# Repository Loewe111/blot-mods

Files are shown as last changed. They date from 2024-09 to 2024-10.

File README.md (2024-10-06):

# My Blot Mods

This is a collection of modifications I've made to my [Blot](https://github.com/hackclub/blot/), a Plotter by Hackclub.

- [Tidy Cable Management](#tidy-cable-management)
- [Limit Switches](#limit-switches)
- [Laser Blot](#laser-blot)

## Tidy Cable Management

I just printed these [Cable Clips](https://www.thingiverse.com/thing:6466108) and secured the cables to it with zip ties.

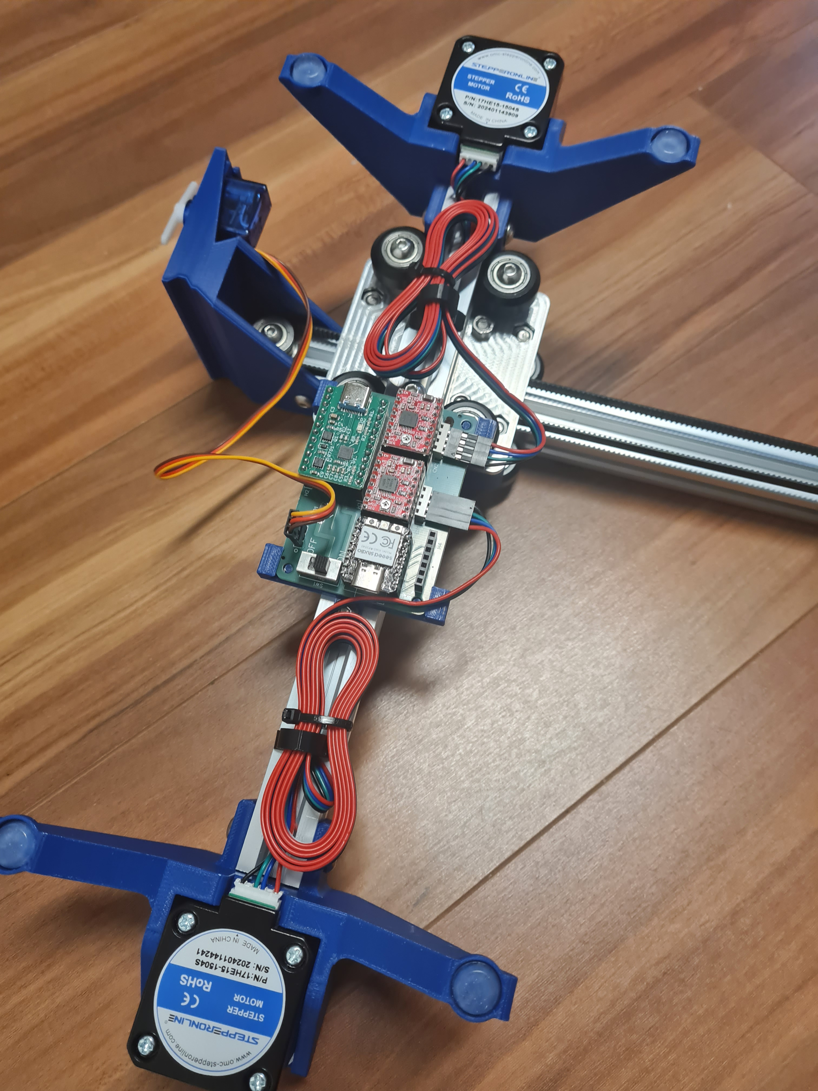
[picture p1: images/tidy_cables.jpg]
Cable Clips


## Limit Switches

This adds a pair of limit switches to the blot, utilizing the header of pins on the PCB.

### Parts

| Quantity | Name | Image |
| --- | --- | --- |
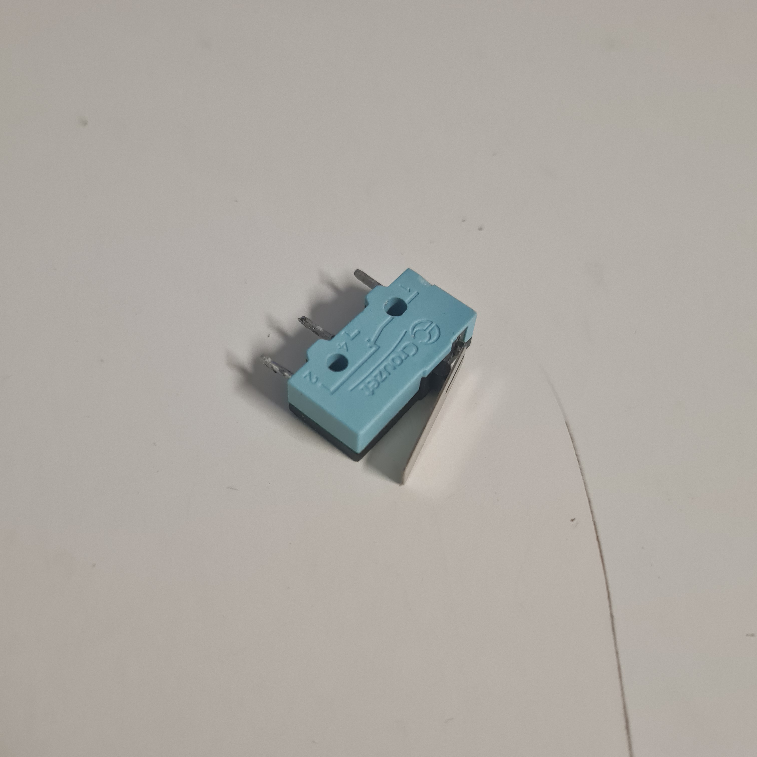
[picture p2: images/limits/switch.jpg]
Limit Switch
| 2 | Limit Switch / Microswitch |  |
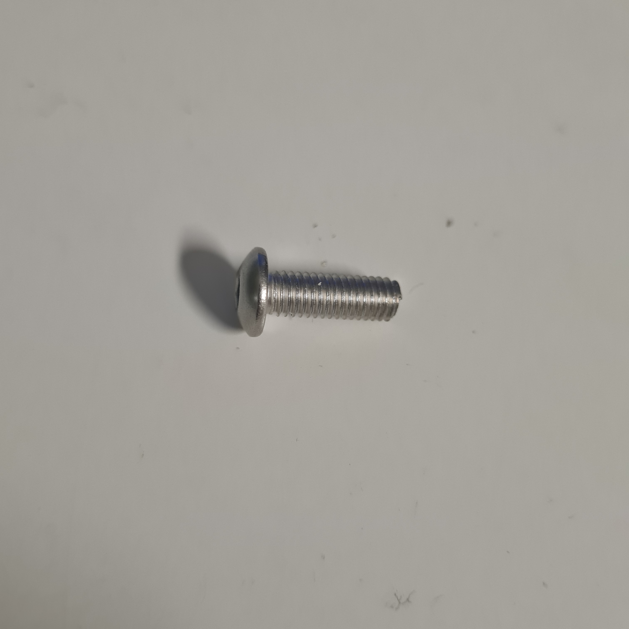
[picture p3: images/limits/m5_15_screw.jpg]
M5x15 Screw
| 1 | M5x15 Screw |  |
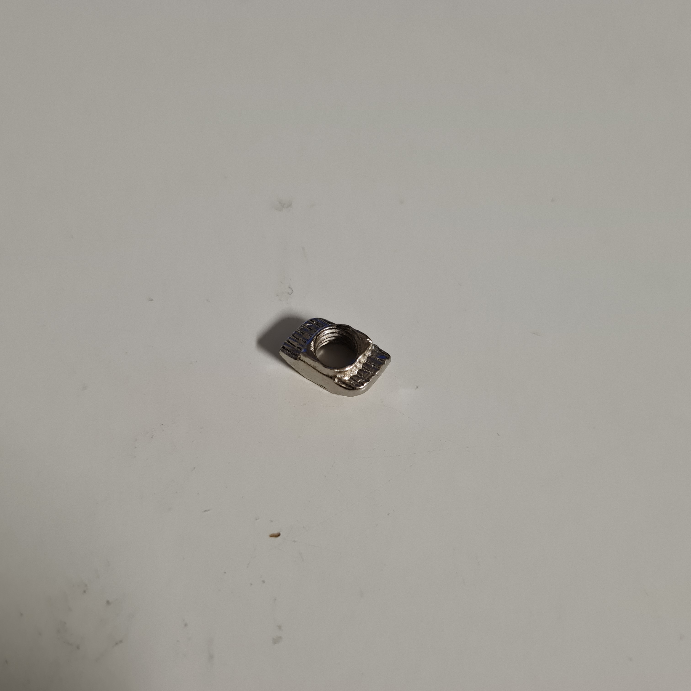
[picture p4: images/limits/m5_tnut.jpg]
M5 T-Nut
| 1 | M5 T-Nut |  |
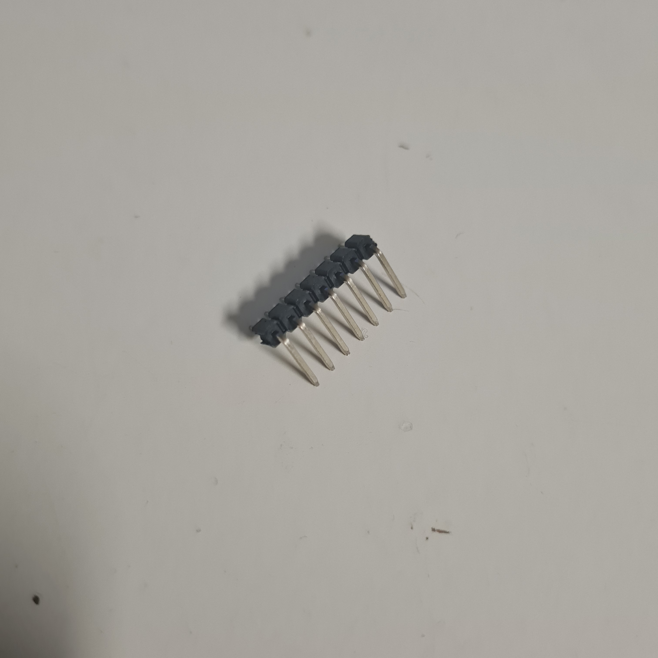
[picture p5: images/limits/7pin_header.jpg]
1x7 Angled Header
| 1 | 1x7 Angled Header |  |
| 4 | ca. 20cm Wire | |
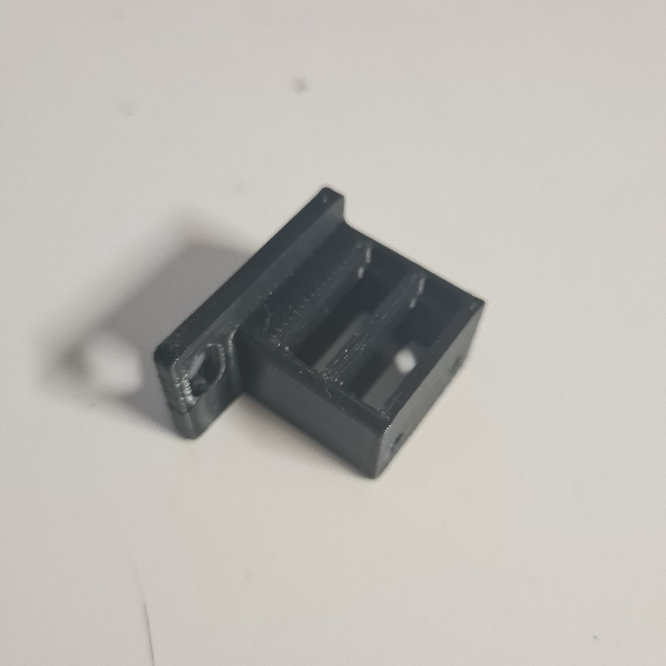
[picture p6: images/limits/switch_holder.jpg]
3D Printed Mount
| 1 | 3D Printed Mount [(here)](models/endstop_mount.stl) |  |
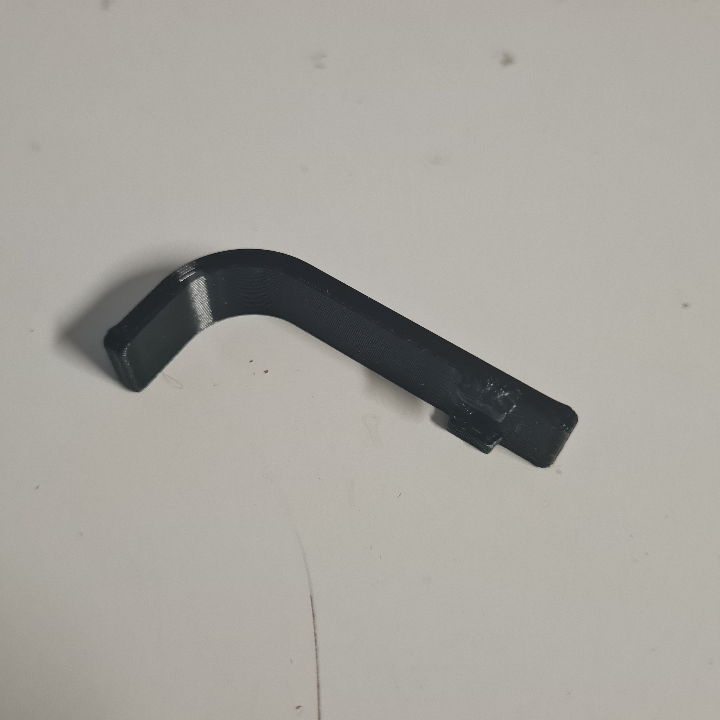
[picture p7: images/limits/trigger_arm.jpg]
3D Printed Arm
| 1 | 3D Printed Arm [(here)](models/endstop_arm.stl) |  |

### Assembly

1. Insert the Limit Switches into the 3D Printed Mount. Make sure the springs face the right direction. Like this:

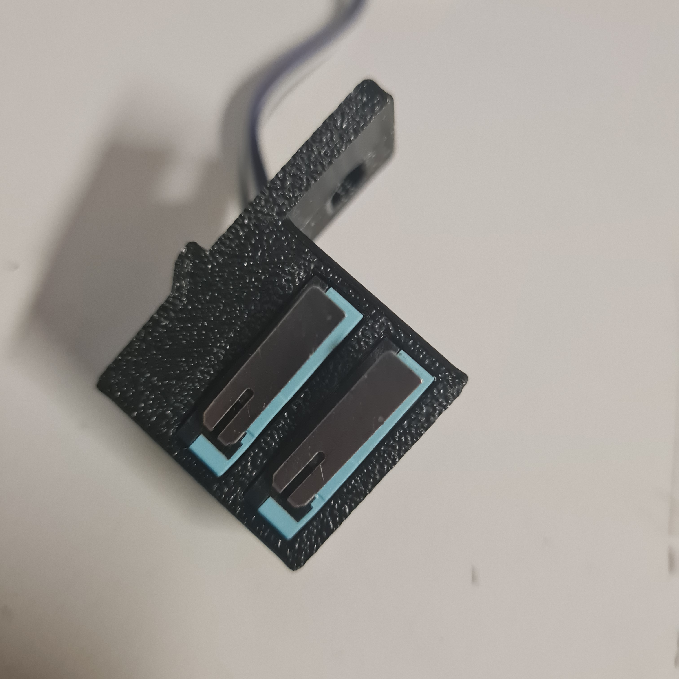
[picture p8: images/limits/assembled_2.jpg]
Assembled
    
2. Solder the Wires to the COM and NC pins of the Limit Switches.
    It should look like this:

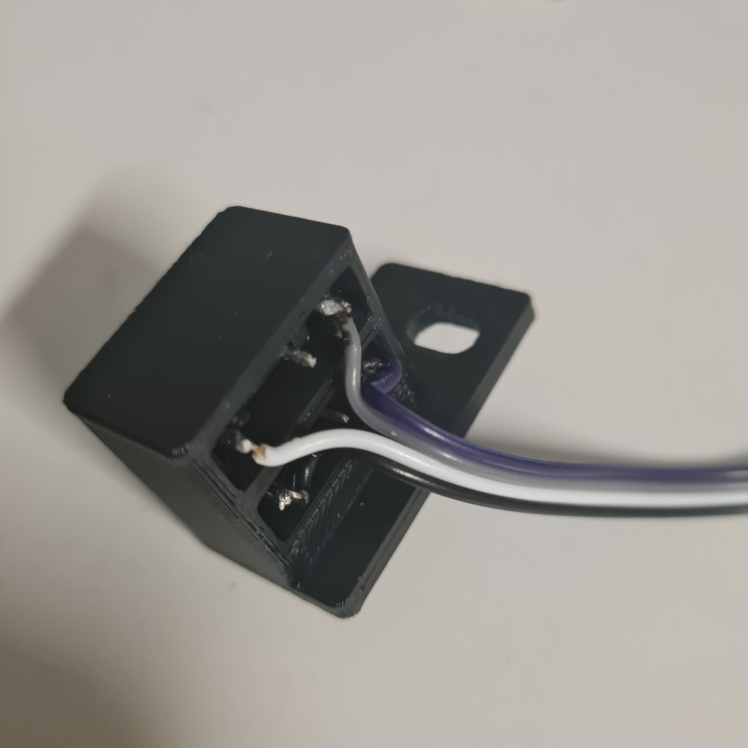
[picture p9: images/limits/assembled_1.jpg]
Wiring
    
3.  Solder the other ends of the wires to the 1x7 Angled Header. The COM pins both connect to 7th pin, the NC pin of the Lower (X) Limit Switch connects to the 3rd pin, and the NC pin of the Upper (Y) Limit Switch connects to the 4th pin.

    Motor Mount
4. Remove the top screw of the left motor mount.

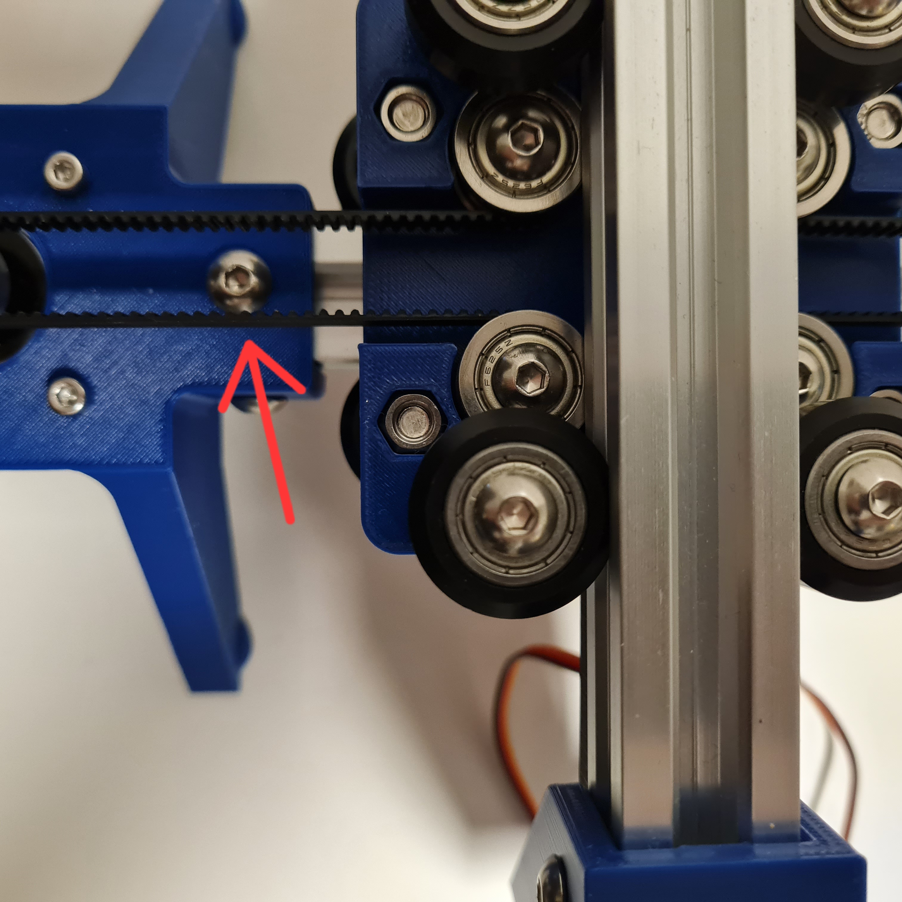
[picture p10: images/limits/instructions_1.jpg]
    

    Then, put the 3D Printed Mount on top of the motor mount and screw it in place with the M5x15 (Keep the old screw for the next step). Adjust the position of the Limit Switches so it gets triggered before the gantry hits the end of the plotter.

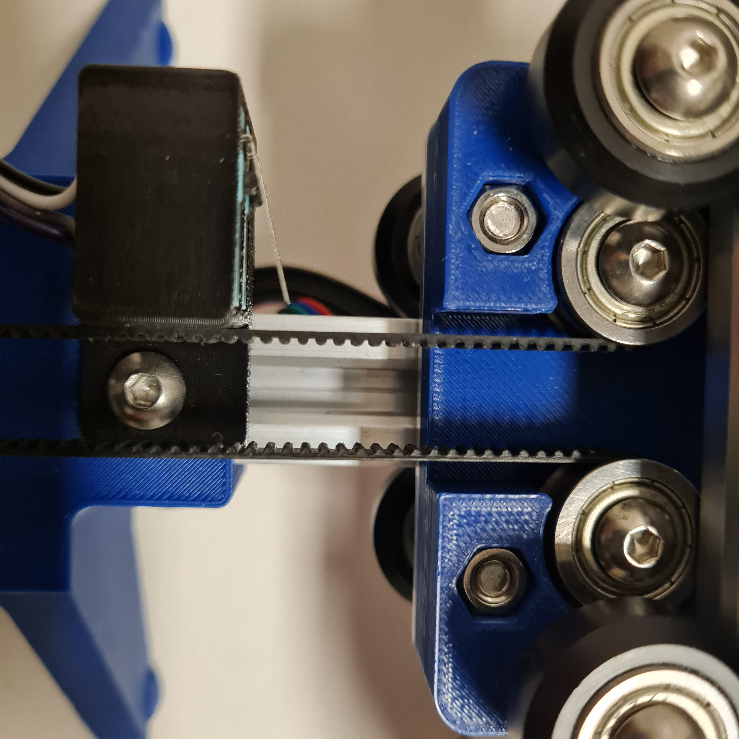
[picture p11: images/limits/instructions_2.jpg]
    
5. Attach the 3D Printed Arm to top extrusion with the M5 T-Nut and the M5x10 screw that you removed in the last step.

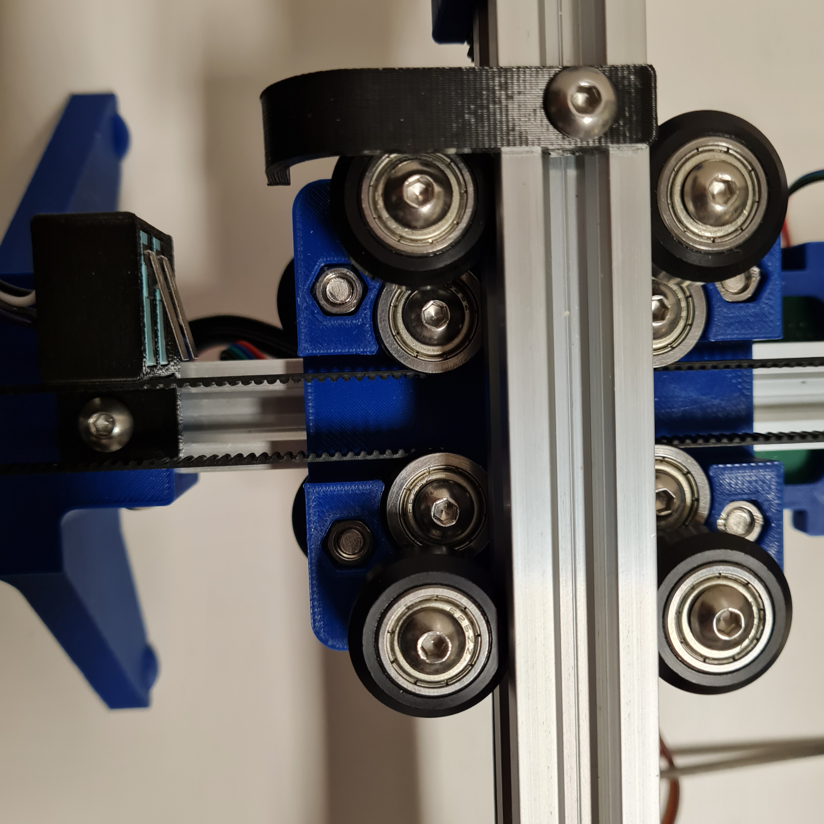
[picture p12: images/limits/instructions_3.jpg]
    

    Make sure that when the gantry is at the limit switch, that the arm also triggers the switch before it hits the end of the plotter.
6. Plug the connector into the header on the PCB.

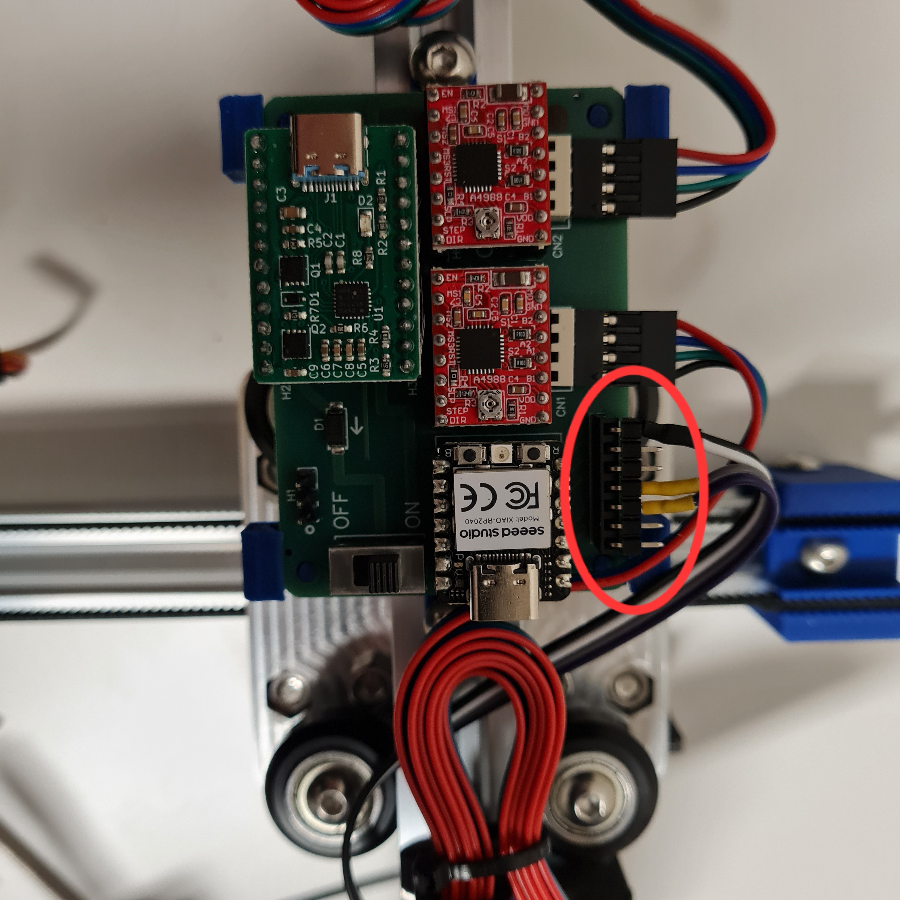
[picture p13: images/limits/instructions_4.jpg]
    

    Make sure the wires are not in the way of the gantry.

That's it!

### Firmware

I have created a grblHAL driver for the Blot. You can find it [here](https://github.com/Loewe111/grblHAL-blot). The only limitation is that it cant use the Servo for the pen lift.

I plan to modify the original firmware to support the limit switches as well.

## Laser Blot

I also added a 5.5W Diode Laser to my Blot. With this I am able to engrave wood, plastics and even acrylics, aswell as cutting paper and some thin wood.

> [!CAUTION]
> Lasers are dangerous! Always wear appropriate eye protection!

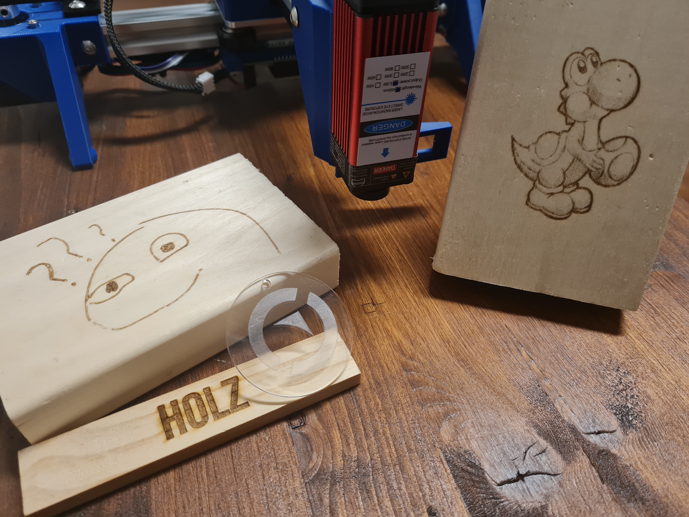
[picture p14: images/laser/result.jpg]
Result


### Parts

| Quantity | Name | Image |
| --- | --- | --- |
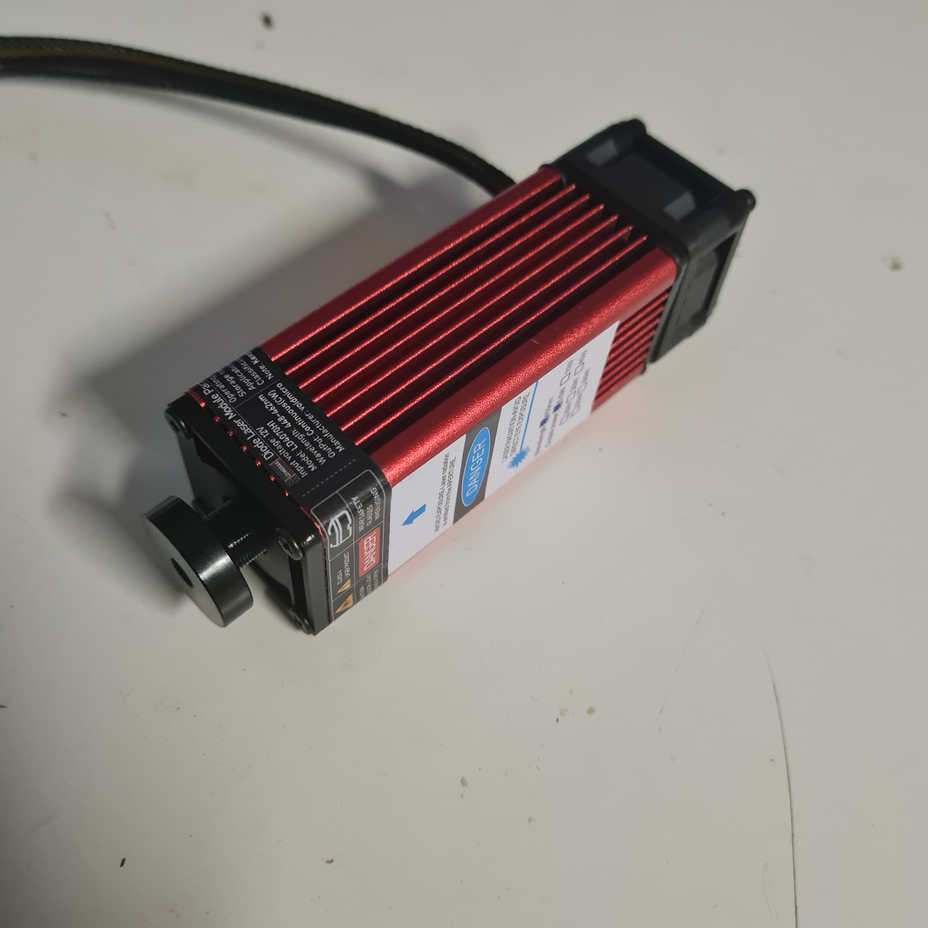
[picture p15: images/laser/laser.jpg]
Laser Module
| 1 | Laser Module (I got [this 5.5W one](https://de.aliexpress.com/item/1005003710714783.html)) |  |
| 1 | Laser Safety Glasses (I got [these](https://www.amazon.de/dp/B0CS6DHZRP)) | |
| 1 | A 12V Power Supply | |
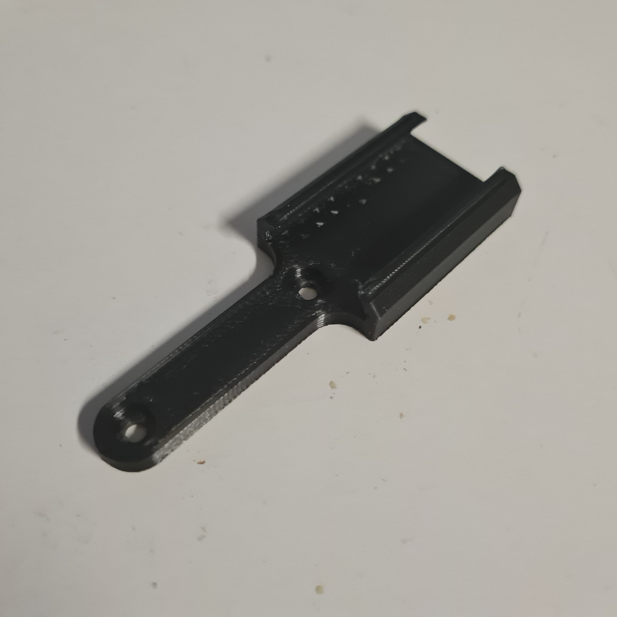
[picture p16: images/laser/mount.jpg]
3D Printed Laser Mount
| 1 | 3D Printed Laser Mount [(here)](models/laser_mount.stl) |   |
| 1 | 12V Barrel Plug (Or other connector for the power supply) | |
| 1 | JST-XH 3 Pin Connector | |
| 1 | 3 Pin Female Header or Crimp Connector | |
| | Some Wires | |

### Assembly

1. Attach the Laser Module to the 3D Printed Mount with the screws that came with the laser.

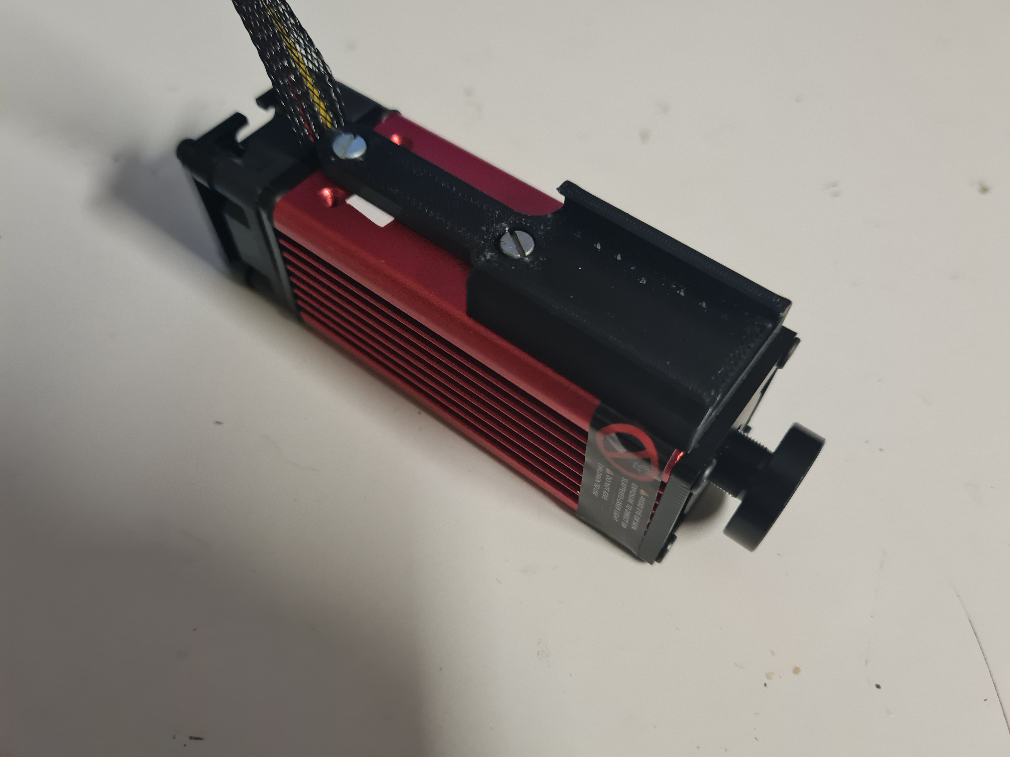
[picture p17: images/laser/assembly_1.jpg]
Laser Assembly
    

2. Create the wiring harness for the laser, by connecting the JST Connector to the Barrel Plug and the 3 Pin Connector as shown in the diagram below.

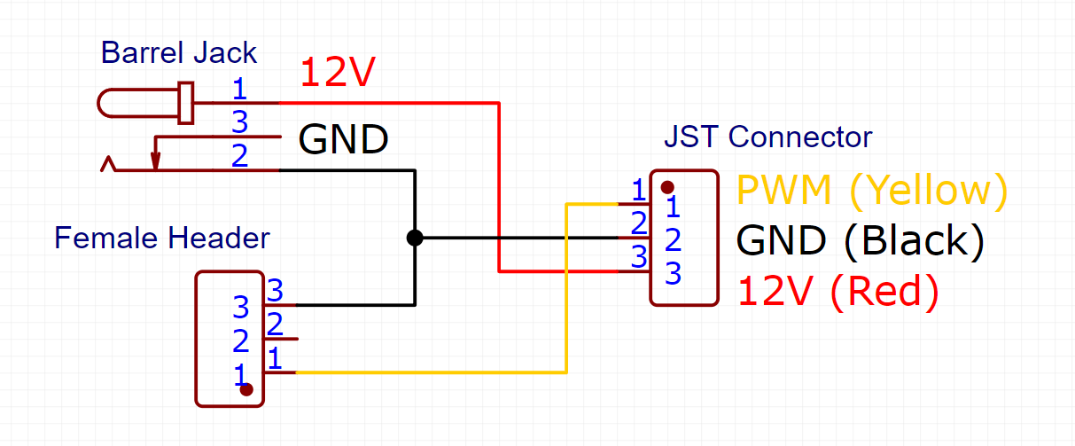
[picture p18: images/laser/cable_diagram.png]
Laser Wiring
    

    My harness looks like this:

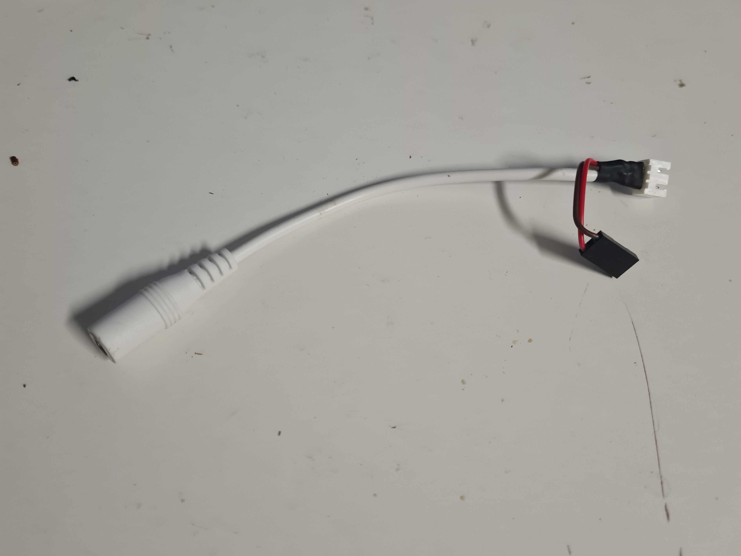
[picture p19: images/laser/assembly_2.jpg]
Laser Wiring
    

3. Connect the 3 Pin Female Header to the Pin Header on the PCB, where the Servo was connected. Make sure that the GND pin is on the side with the white dot.

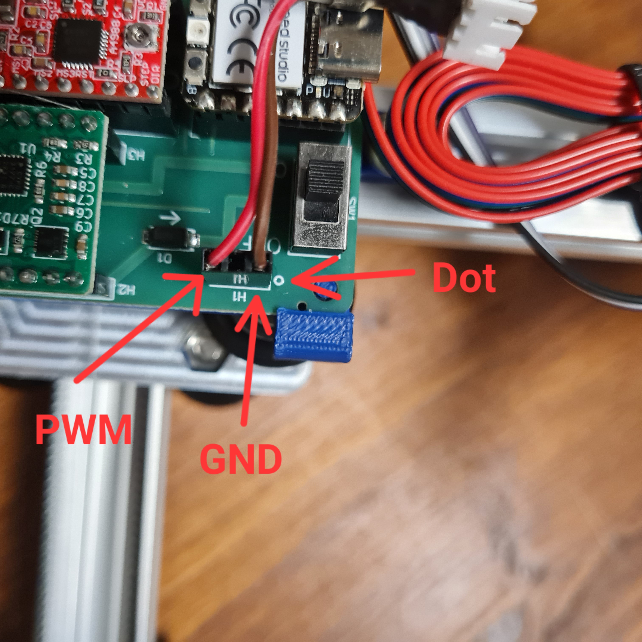
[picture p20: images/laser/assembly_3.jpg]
Laser Wiring
    

4. Attach the Laser to the Arm, where the Pen Holder was attached.

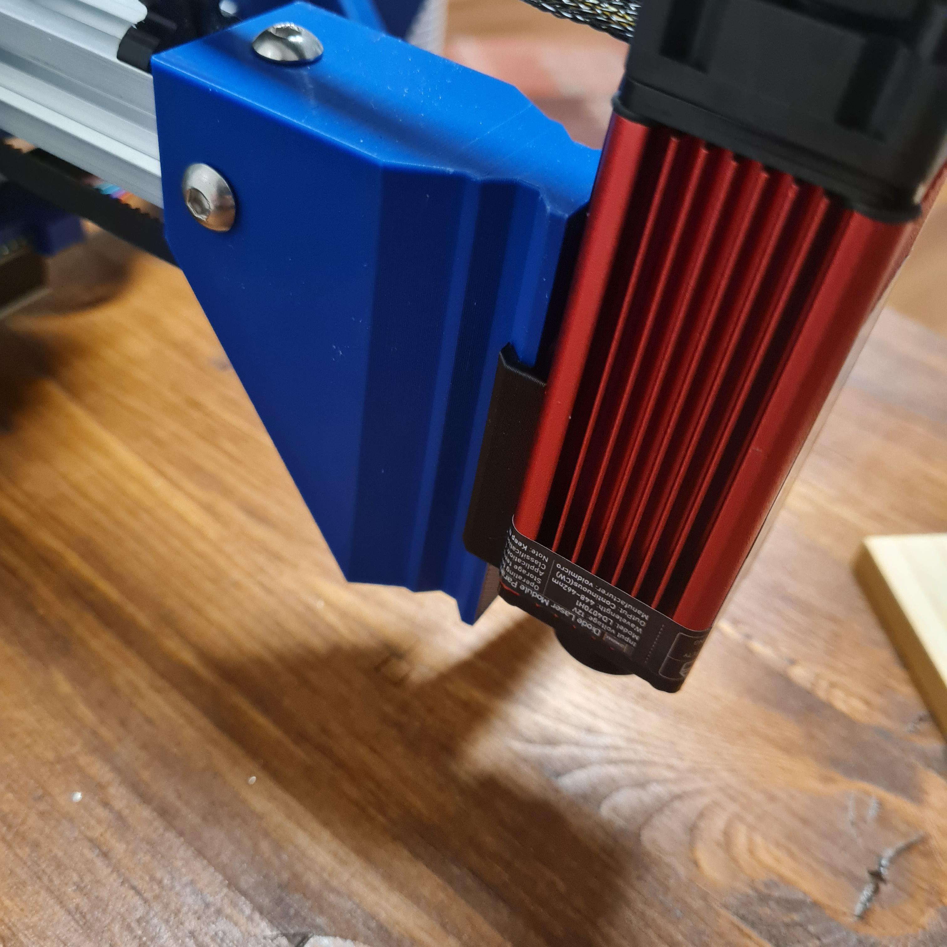
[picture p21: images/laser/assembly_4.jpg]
Laser Assembly
    

    I also removed the Servo, but you can keep it if you want to use it in the future.

5. Connect the Laser to your Wiring Harness.

### Software

I use my [GrblHAL driver](https://github.com/Loewe111/grblHAL-blot) on the Blot, paired with [LightBurn](https://lightburnsoftware.com/) for the laser control.

Configure the driver with the following settings:

```gcode
$9=1
$30=1000
$31=0
$33=5000
$32=1
$110=8000
$111=8000
```

If you also have the limit switches installed (which I highly recommend), also set the following:

```gcode
$22=9
```

Otherwise you will have to manually set the origin with `G92X0Y0` before every job.

### Usage

Always wear the Laser Safety Glasses when the laser is on!

My workflow is as follows:

1. Home the machine.
2. Create my design in LightBurn.
3. Use the "Frame" function to align the design with the material.
4. Start the job.

---

Some of my settings with my 5.5W Laser

| Material | Speed (mm/min) | Power (%) |
| --- | --- | --- |
| Wood | 750 | 100 |
| Acrylic | 500 | 50 |
| PLA | 1000 | 100 |

> [!TIP]
> When engraving Acrylic, I first cover the surface with black Whiteboard Marker and then wipe it off after engraving. This gives the laser a surface to engrave on, since it would just pass through the clear acrylic.

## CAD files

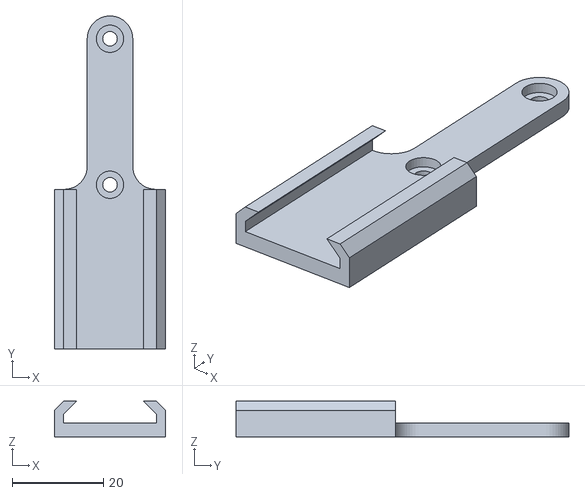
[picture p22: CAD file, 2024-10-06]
models/laser_mount.stl
24.4 x 73.0 x 7.83

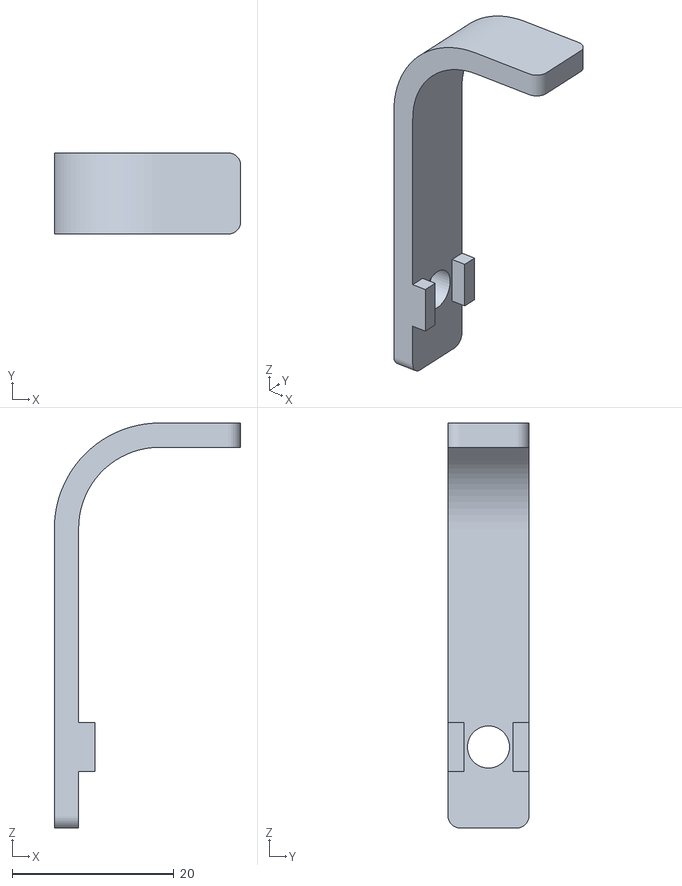
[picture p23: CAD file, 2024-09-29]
models/endstop_arm.stl
23.0 x 10.0 x 50.0

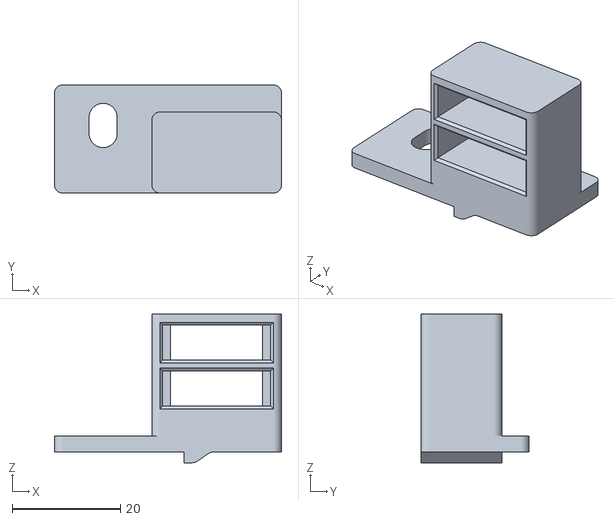
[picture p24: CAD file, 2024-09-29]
models/endstop_mount.stl
42.0 x 20.0 x 27.5
